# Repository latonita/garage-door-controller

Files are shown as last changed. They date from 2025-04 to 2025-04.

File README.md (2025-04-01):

# garage-door-controller
Garage door controller with integrated motor driver 24V/36V, 7A

Features:
- DRV8701 driver
   - selectable mosfet gate drive
   - and overcurrent protection
- PowerSO mosfets
  - shall be enough to run 24V/7A and more
- External interface for common RF-receivers
  - RX-480R / RF11A04 
  - HCS301 based
- Fabrication
  - Prepared for automated assembly on JLCPCB
  - Most of components are basic, no unnesessary Pick-and-place feeding fees. I personally order only couple of Extended parts to be soldered.

# under construction

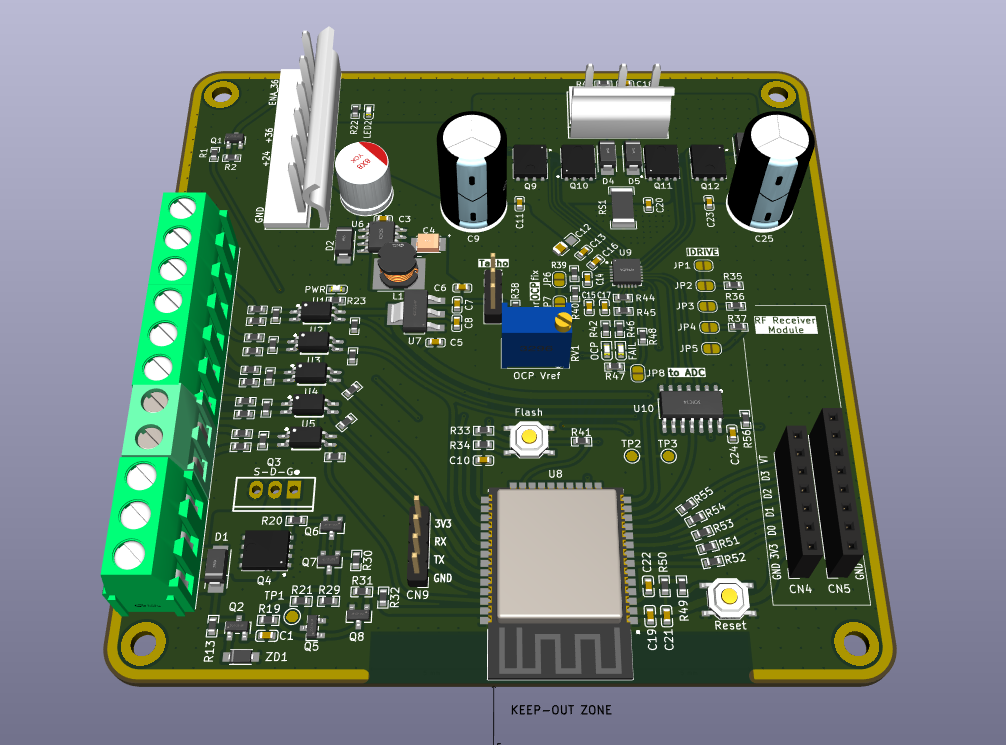
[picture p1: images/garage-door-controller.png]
Garage door controller PCB


# BOM

[Interactive BOM](https://raw.githack.com/latonita/garage-door-controller/refs/heads/main/kicad-project/bom/ibom.html)

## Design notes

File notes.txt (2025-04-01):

Tracks
 - signals mostly 0.25mm, some longer 0.3mm
 - power 0.5mm mostly

Clearance
 - 36V(VM) and motor planes - 0.6mm
 - GND 0.4mm

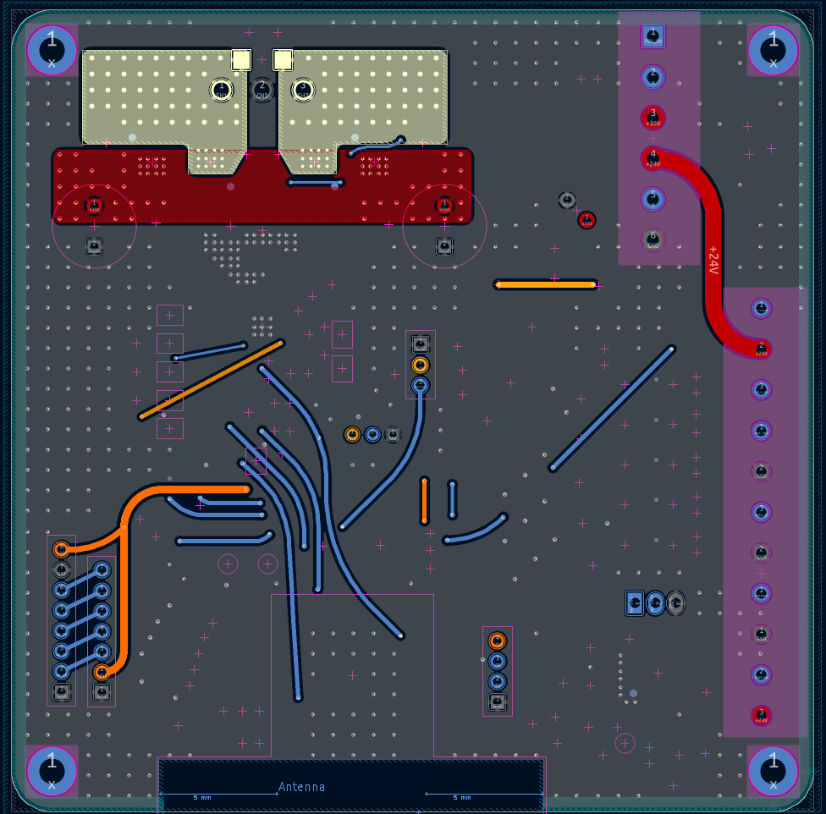
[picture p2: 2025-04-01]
images/pcb-bottom.png

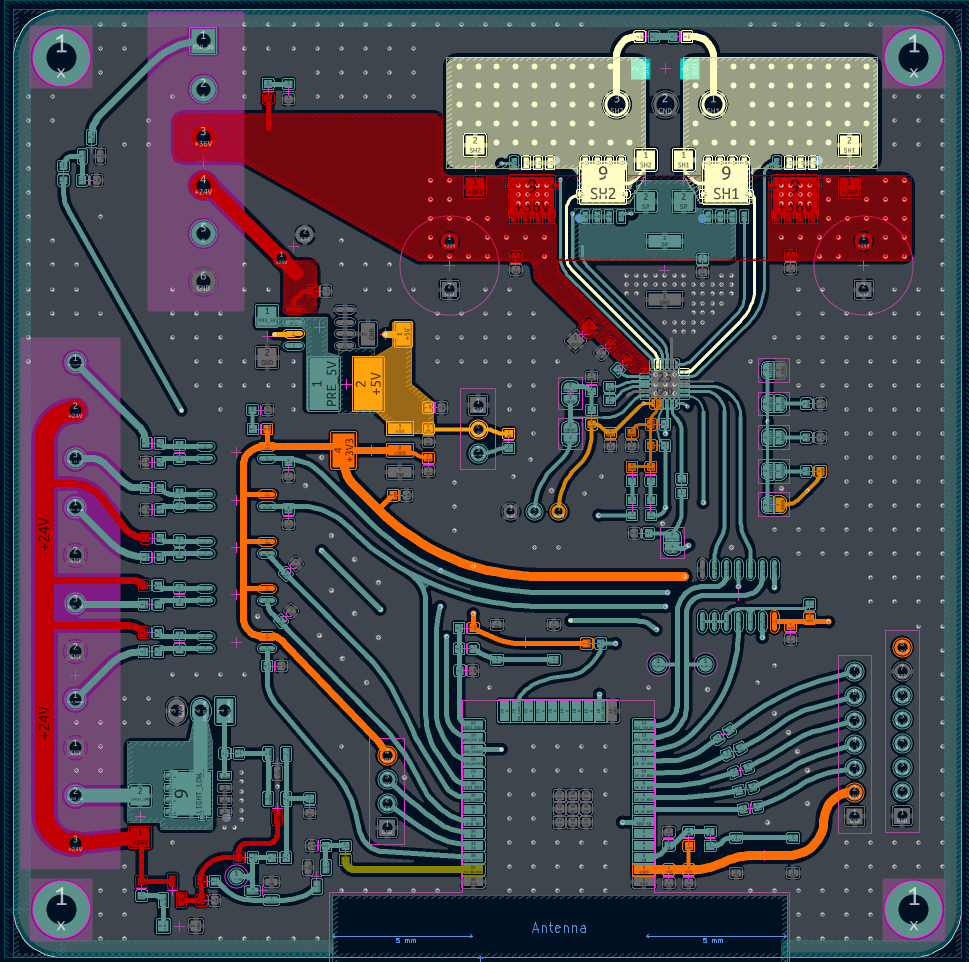
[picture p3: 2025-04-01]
images/pcb-top.png

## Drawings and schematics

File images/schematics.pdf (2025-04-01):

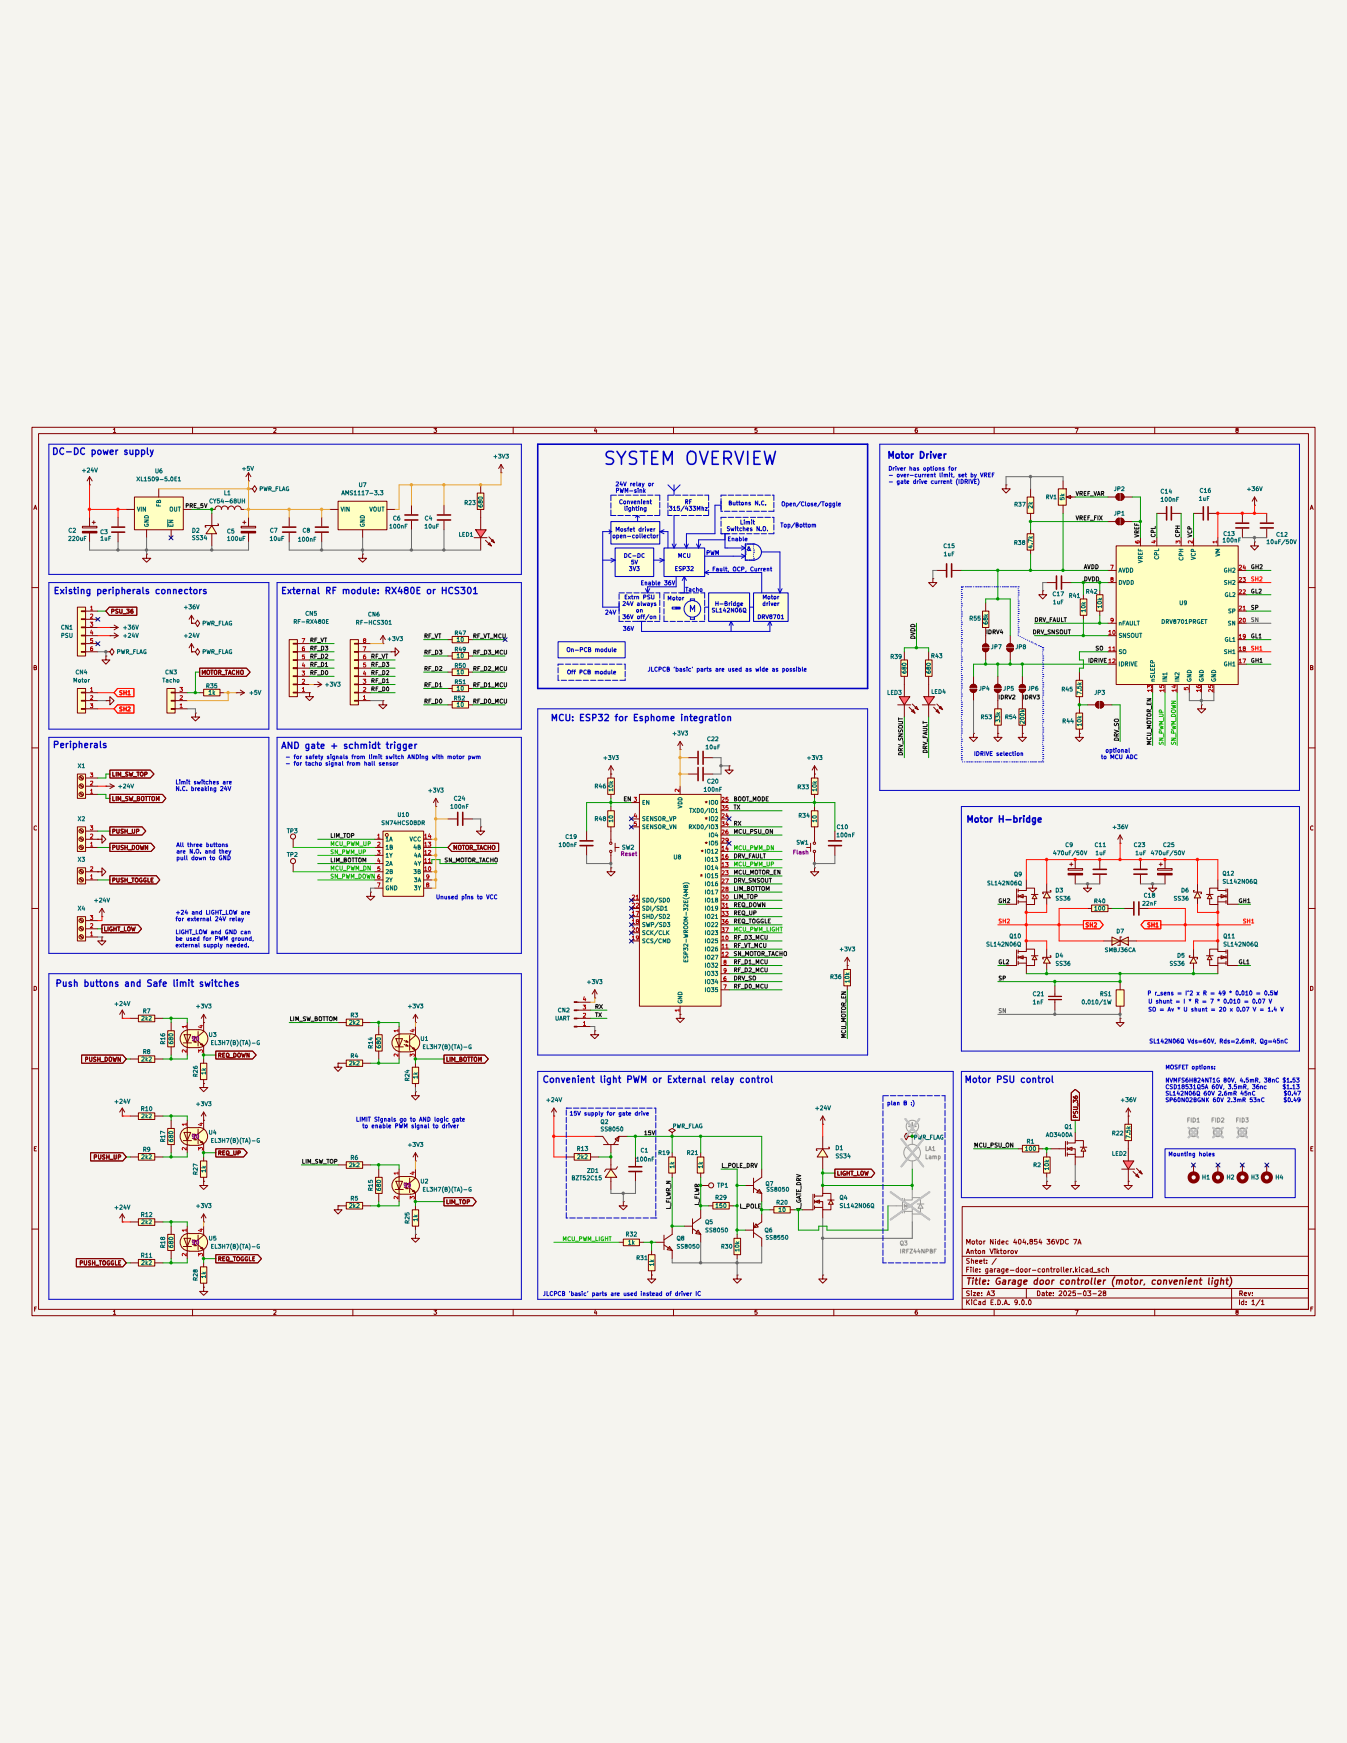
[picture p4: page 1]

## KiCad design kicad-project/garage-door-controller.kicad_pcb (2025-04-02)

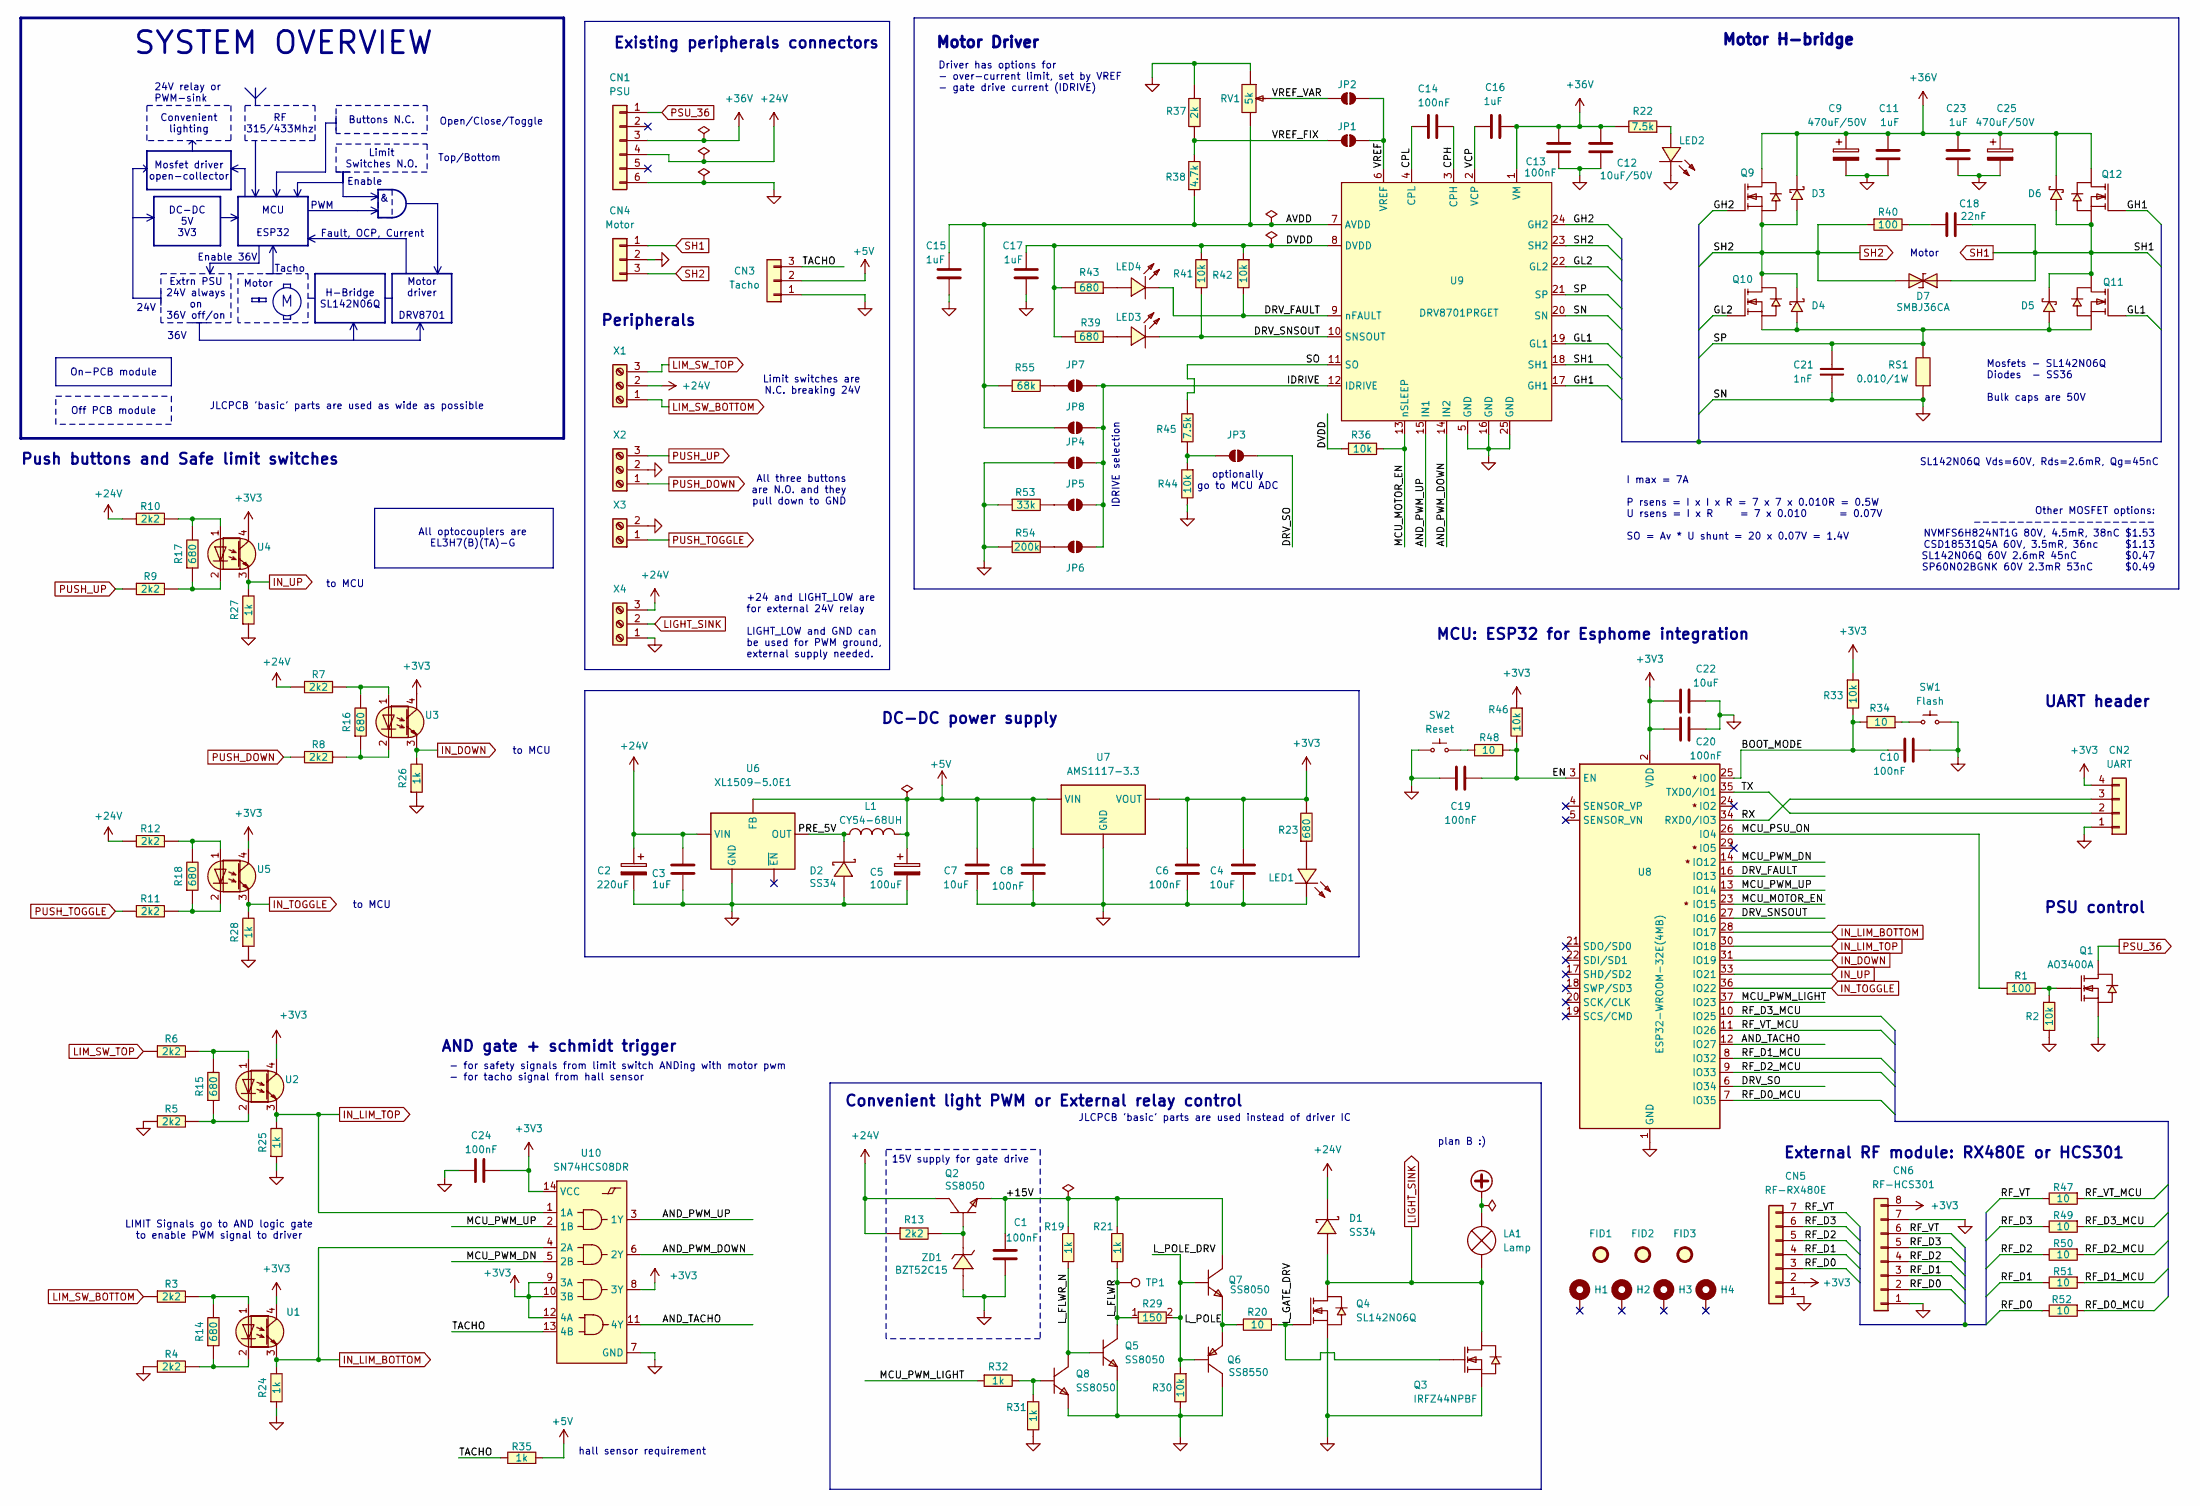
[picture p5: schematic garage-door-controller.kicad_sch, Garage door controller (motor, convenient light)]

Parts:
C1, C6, C8, C10, C13, C14, C19, C20, C24: 100nF; C0603; LCSC Part C14663
C2: 220uF; CAP-TH_BD8.0-P3.50-D0.6-FD; LCSC Part C106697
C3, C11, C15, C16, C17, C23: 1uF; C0603; LCSC Part C15849
C4, C7, C22: 10uF; C0603; LCSC Part C19702
C5: 100uF; CASE-B_3528; LCSC Part C16133
C9, C25: 470uF/50V; CAP-TH_BD10.0-P5.00-D1.0-FD; LCSC Part C88733
C12: 10uF/50V; C0805; LCSC Part C440198
C18: 22nF; C0603; LCSC Part C21122
C21: 1nF; C0603; LCSC Part C1588
CN1: PSU; CONN-TH_6P-P5.08_CH5.08-6A; LCSC Part C76512
CN2: UART; PinHeader_1x04_P2.54mm_Vertical
CN3: Tacho; PinHeader_1x03_P2.54mm_Vertical
CN4: Motor; CONN-TH_CH5.08-3A; LCSC Part C23514
CN5: RF-RX480E; PinSocket_1x07_P2.54mm_Vertical; LCSC Part C22438157
CN6: RF-HCS301; PinSocket_1x08_P2.54mm_Vertical; LCSC Part C27438
D1, D2: SS34; SMA_L4.3-W2.6-LS5.2-RD; LCSC Part C8678
D3, D4, D5, D6: SS36; SMA_L4.3-W2.6-LS5.2-RD; LCSC Part C16015
D7: SMBJ36CA; SMB_L4.6-W3.6-LS5.3-BI; LCSC Part C78421
FID1, FID2, FID3: Fiducial; Fiducial_1mm_Mask2mm
H1, H2, H3, H4: MountingHole; MountingHole_3.2mm_M3_DIN965_Pad
JP1, JP2, JP3, JP4, JP5, JP6, JP7, JP8: SolderJumper_2_Open; SolderJumper-2_P1.3mm_Open_RoundedPad1.0x1.5mm
L1: CY54-68UH; IND-SMD_L5.8-W5.2; LCSC Part C2929435
LA1: Lamp
LED1, LED2, LED3, LED4: KT-0603R; LED0603-RD; LCSC Part C2286
Q1: AO3400A; SOT-23-3_L2.9-W1.3-P1.90-LS2.4-BR; LCSC Part C20917
Q2, Q5, Q7, Q8: SS8050; SOT-23-3_L2.9-W1.3-P1.90-LS2.4-BR; LCSC Part C2150
Q3: IRFZ44NPBF; TO-220-3_L10.0-W4.5-P2.54-L; LCSC Part C2586
Q4, Q9, Q10, Q11, Q12: SL142N06Q; PDFN-8_L5.9-W5.2-P1.27-LS6.2-BL; LCSC Part C18208610
Q6: SS8550; SOT-23-3_L2.9-W1.3-P1.90-LS2.4-BR; LCSC Part C8542
R1, R40: 100; R0603; LCSC Part C22775
R2, R30, R33, R36, R41, R42, R44, R46: 10k; R0603; LCSC Part C25804
R3, R4, R5, R6, R7, R8, R9, R10, R11, R12, R13: 2k2; R0603; LCSC Part C4190
R14, R15, R16, R17, R18, R23, R39, R43: 680; R0603; LCSC Part C23228
R19, R21, R24, R25, R26, R27, R28, R31, R32, R35: 1k; R0603; LCSC Part C21190
R20, R34, R47, R48, R49, R50, R51, R52: 10; R0603; LCSC Part C22859
R22, R45: 7.5k; R0603; LCSC Part C23234
R29: 150; R0603; LCSC Part C22808
R37: 2k; R0603; LCSC Part C22975
R38: 4.7k; R0603; LCSC Part C23162
R53: 33k; R0603; LCSC Part C4216
R54: 200k; R0603; LCSC Part C25811
R55: 68k; R0603; LCSC Part C23231
RS1: 0.010/1W; R2512; LCSC Part C393072
RV1: 5k; RES-ADJ-TH_3296W; LCSC Part C60620
SW1, SW2: TS-1187A-B-A-B; SW-SMD_4P-L5.1-W5.1-P3.70-LS6.5-TL_H1.5; LCSC Part C318884
TP1: TestPoint; TestPoint_Pad_D1.5mm
U1, U2, U3, U4, U5: EL3H7(B)(TA)-G; SOP-4_L4.4-W2.8-P1.27-LS7.0-TL; LCSC Part C32565
U6: XL1509-5.0E1; SOIC-8_L5.0-W4.0-P1.27-LS6.0-BL; LCSC Part C61063
U7: AMS1117-3.3; SOT-223-3_L6.5-W3.4-P2.30-LS7.0-BR; LCSC Part C6186
U8: ESP32-WROOM-32E(4MB); WIFI-SMD_ESP32-WROOM-32E; LCSC Part C701341
U9: DRV8701PRGET; VQFN-24_L4.0-W4.0-P0.50-TL-EP2.8; LCSC Part C2150478
U10: SN74HCS08DR; SOIC-14_L8.7-W3.9-P1.27-LS6.0-BL; LCSC Part C2868021
X1, X2, X4: WJ500V-5.08-3P-14-00A; CONN-TH_3P-P5.00_WJ500V-5.08-3P; LCSC Part C72334
X3: WJ500V-5.08-2P-14-00A; CONN-TH_2P-P5.00_WJ500V-5.08-2P; LCSC Part C8465
ZD1: BZT52C15; SOD-123_L2.7-W1.6-LS3.8-RD; LCSC Part C2932746

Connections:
+3V3: C4.2, C6.2, C20.1, C22.1, C24.1, CN2.4, CN5.2, CN6.8, R23.2, R33.1, R46.1, U1.4, U2.4, U3.4, U4.4, U5.4, U7.2 (VOUT), U7.4 (TAB), U8.2 (VDD), U10.8 (3Y), U10.9 (3A), U10.10 (3B), U10.12 (4A), U10.14 (VCC)
+5V: C5.1, C7.2, C8.2, CN3.2, L1.2, R35.1, U6.3 (FB), U7.3 (VIN)
+24V: C2.1, C3.2, CN1.4, D1.1 (K), Q2.3 (C), R7.1, R10.1, R12.1, R13.1, U6.1 (VIN), X1.2, X4.3
+36V: C9.1, C11.2, C12.2, C13.1, C16.2, C23.2, C25.1, CN1.3, D3.1 (K), D6.1 (K), Q9.5 (D), Q9.6 (D), Q9.7 (D), Q9.8 (D), Q9.9 (D), Q12.5 (D), Q12.6 (D), Q12.7 (D), Q12.8 (D), Q12.9 (D), R22.2, U9.1 (VM)
/+15V: C1.2, Q2.2 (E), Q7.3 (C), R19.2, R21.2
/AND_PWM_DOWN: U9.14 (IN2), U10.6 (2Y)
/AND_PWM_UP: U9.15 (IN1), U10.3 (1Y)
/AND_TACHO: U8.12 (IO27), U10.11 (4Y)
/AVDD: C15.2, JP8.1 (A), R38.1, R55.1, RV1.1, U9.7 (AVDD)
/BOOT_MODE: C10.1, R33.2, R34.2, U8.25 (IO0)
/CPH: C14.1, U9.3 (CPH)
/CPL: C14.2, U9.4 (CPL)
/DRV_FAULT: LED4.1 (K), R42.2, U8.16 (IO13), U9.9 (nFAULT)
/DRV_SNSOUT: LED3.1 (K), R41.2, U8.27 (IO16), U9.10 (SNSOUT)
/DRV_SO: JP3.1 (A), U8.6 (IO34)
/DVDD: C17.2, R36.1, R39.2, R41.1, R42.1, R43.2, U9.8 (DVDD)
/EN: C19.1, R46.2, R48.1, U8.3 (EN)
/GH1: Q12.4 (G), U9.17 (GH1)
/GH2: Q9.4 (G), U9.24 (GH2)
/GL1: Q11.4 (G), U9.19 (GL1)
/GL2: Q10.4 (G), U9.22 (GL2)
/IDRIVE: JP4.2 (B), JP5.2 (B), JP6.2 (B), JP7.2 (B), JP8.2 (B), U9.12 (IDRIVE)
/L_FLWR: Q5.3 (C), R21.1, R29.1, TP1.1
/L_FLWR_N: Q5.1 (B), Q8.3 (C), R19.1
/L_GATE_DRV: Q3.1 (G), Q4.4 (G), R20.1
/L_POLE: Q6.2 (E), Q7.2 (E), R20.2
/L_POLE_DRV: Q6.1 (B), Q7.1 (B), R29.2, R30.1
/MCU_MOTOR_EN: R36.2, U8.23 (IO15), U9.13 (nSLEEP)
/MCU_PSU_ON: R1.1, U8.26 (IO4)
/MCU_PWM_DN: U8.14 (IO12), U10.5 (2B)
/MCU_PWM_LIGHT: R32.1, U8.37 (IO23)
/MCU_PWM_UP: U8.13 (IO14), U10.2 (1B)
/PRE_5V: D2.1 (K), L1.1, U6.2 (OUT)
/RF_D0: CN5.3, CN6.2, R52.2
/RF_D0_MCU: R52.1, U8.7 (IO35)
/RF_D1: CN5.4, CN6.3, R51.2
/RF_D1_MCU: R51.1, U8.8 (IO32)
/RF_D2: CN5.5, CN6.4, R50.2
/RF_D2_MCU: R50.1, U8.9 (IO33)
/RF_D3: CN5.6, CN6.5, R49.2
/RF_D3_MCU: R49.1, U8.10 (IO25)
/RF_VT: CN5.7, CN6.6, R47.2
/RF_VT_MCU: R47.1, U8.11 (IO26)
/RX: CN2.3, U8.34 (RXD0/IO3)
/SO: R45.2, U9.11 (SO)
/SP: C21.2, D4.2 (A), D5.2 (A), Q10.1 (S), Q10.2 (S), Q10.3 (S), Q11.1 (S), Q11.2 (S), Q11.3 (S), RS1.2, U9.21 (SP)
/TACHO: CN3.3, R35.2, U10.13 (4B)
/TX: CN2.2, U8.35 (TXD0/IO1)
/VCP: C16.1, U9.2 (VCP)
/VREF: JP1.2 (B), JP2.2 (B), U9.6 (VREF)
/VREF_FIX: JP1.1 (A), R37.2, R38.2
/VREF_VAR: JP2.1 (A), RV1.2
GND: C1.1, C2.2, C3.1, C4.1, C5.2, C6.1, C7.1, C8.1, C9.2, C10.2, C11.1, C12.1, C13.2, C15.1, C17.1, C19.2, C20.2, C21.1, C22.2, C23.1, C24.2, C25.2, CN1.6, CN2.1, CN3.1, CN4.2, CN5.1, CN6.1, CN6.7, D2.2 (A), JP4.1 (A), LED1.1 (K), LED2.1 (K), Q1.2 (S), Q3.3 (S), Q4.1 (S), Q4.2 (S), Q4.3 (S), Q5.2 (E), Q6.3 (C), Q8.2 (E), R2.2, R4.1, R5.1, R24.1, R25.1, R26.1, R27.1, R28.1, R30.2, R31.1, R37.1, R44.2, R53.1, R54.1, RS1.1, RV1.3, SW1.1 (A), SW1.2 (B), SW2.1 (A), SW2.2 (B), U6.5 (GND), U6.6 (GND), U6.7 (GND), U6.8 (GND), U7.1 (GND), U8.1 (GND), U8.15 (GND), U8.38 (GND), U8.39 (GND), U9.5 (GND), U9.16 (GND), U9.20 (SN), U9.25 (GND), U10.7 (GND), X2.2, X3.2, X4.1, ZD1.2 (A)
IN_DOWN: R26.2, U3.3, U8.31 (IO19)
IN_LIM_BOTTOM: R24.2, U1.3, U8.28 (IO17), U10.4 (2A)
IN_LIM_TOP: R25.2, U2.3, U8.30 (IO18), U10.1 (1A)
IN_TOGGLE: R28.2, U5.3, U8.36 (IO22)
IN_UP: R27.2, U4.3, U8.33 (IO21)
LIM_SW_BOTTOM: R3.1, X1.1
LIM_SW_TOP: R6.1, X1.3
unnamed: C18.1, R40.2
unnamed: JP3.2 (B), R44.1, R45.1
unnamed: JP5.1 (A), R53.2
unnamed: JP6.1 (A), R54.2
unnamed: JP7.1 (A), R55.2
unnamed: LED1.2 (A), R23.1
unnamed: LED2.2 (A), R22.1
unnamed: LED3.2 (A), R39.1
unnamed: LED4.2 (A), R43.1
unnamed: Q1.1 (G), R1.2, R2.1
unnamed: Q2.1 (B), R13.2, ZD1.1 (K)
unnamed: Q8.1 (B), R31.2, R32.2
unnamed: R10.2, R17.2, U4.1
unnamed: R11.2, R18.1, U5.2
unnamed: R12.2, R18.2, U5.1
unnamed: R4.2, R14.1, U1.2
unnamed: R3.2, R14.2, U1.1
unnamed: R5.2, R15.1, U2.2
unnamed: R6.2, R15.2, U2.1
unnamed: R8.2, R16.1, U3.2
unnamed: R7.2, R16.2, U3.1
unnamed: R9.2, R17.1, U4.2
unnamed: R34.1, SW1.3 (C), SW1.4 (D)
unnamed: R48.2, SW2.3 (C), SW2.4 (D)
PSU_36: CN1.1, Q1.3 (D)
PUSH_DOWN: R8.1, X2.1
PUSH_TOGGLE: R11.1, X3.1
PUSH_UP: R9.1, X2.3
SH1: C18.2, CN4.1, D5.1 (K), D6.2 (A), D7.1 (K), Q11.5 (D), Q11.6 (D), Q11.7 (D), Q11.8 (D), Q11.9 (D), Q12.1 (S), Q12.2 (S), Q12.3 (S), U9.18 (SH1)
SH2: CN4.3, D3.2 (A), D4.1 (K), D7.2 (A), Q9.1 (S), Q9.2 (S), Q9.3 (S), Q10.5 (D), Q10.6 (D), Q10.7 (D), Q10.8 (D), Q10.9 (D), R40.1, U9.23 (SH2)

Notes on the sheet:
JLCPCB 'basic' parts are used as wide as possible
All optocouplers are EL3H7(B)(TA)-G
Motor H-bridge
Top/Bottom
Enable
Other MOSFET options: --------------------- NVMFS6H824NT1G 80V, 4.5mR, 38nC $1.53 CSD18531Q5A 60V, 3.5mR, 36nc $1.13 SL142N06Q 60V 2.6mR 45nC $0.47 SP60N02BGNK 60V 2.3mR 53nC $0.49
IDRIVE selection
DC-DC power supply
Peripherals
Tacho
36V
PSU control
hall sensor requirement
to MCU
JLCPCB 'basic' parts are used instead of driver IC
Motor
Enable 36V
SYSTEM OVERVIEW
Existing peripherals connectors
All three buttons are N.O. and they pull down to GND
MCU: ESP32 for Esphome integration
plan B :)
optionally go to MCU ADC
Driver has options for - over-current limit, set by VREF - gate drive current (IDRIVE)
PWM
Fault, OCP, Current
Mosfets - SL142N06Q Diodes - SS36 Bulk caps are 50V
Convenient light PWM or External relay control
+24 and LIGHT_LOW are for external 24V relay LIGHT_LOW and GND can be used for PWM ground, external supply needed.
UART header
Limit switches are N.C. breaking 24V
Open/Close/Toggle
SL142N06Q Vds=60V, Rds=2.6mR, Qg=45nC
AND gate + schmidt trigger
External RF module: RX480E or HCS301
24V relay or PWM-sink
- for safety signals from limit switch ANDing with motor pwm - for tacho signal from hall sensor
24V
I max = 7A P rsens = I x I x R = 7 x 7 x 0.010R = 0.5W U rsens = I x R = 7 x 0.010 = 0.07V SO = Av * U shunt = 20 x 0.07V = 1.4V
LIMIT Signals go to AND logic gate to enable PWM signal to driver

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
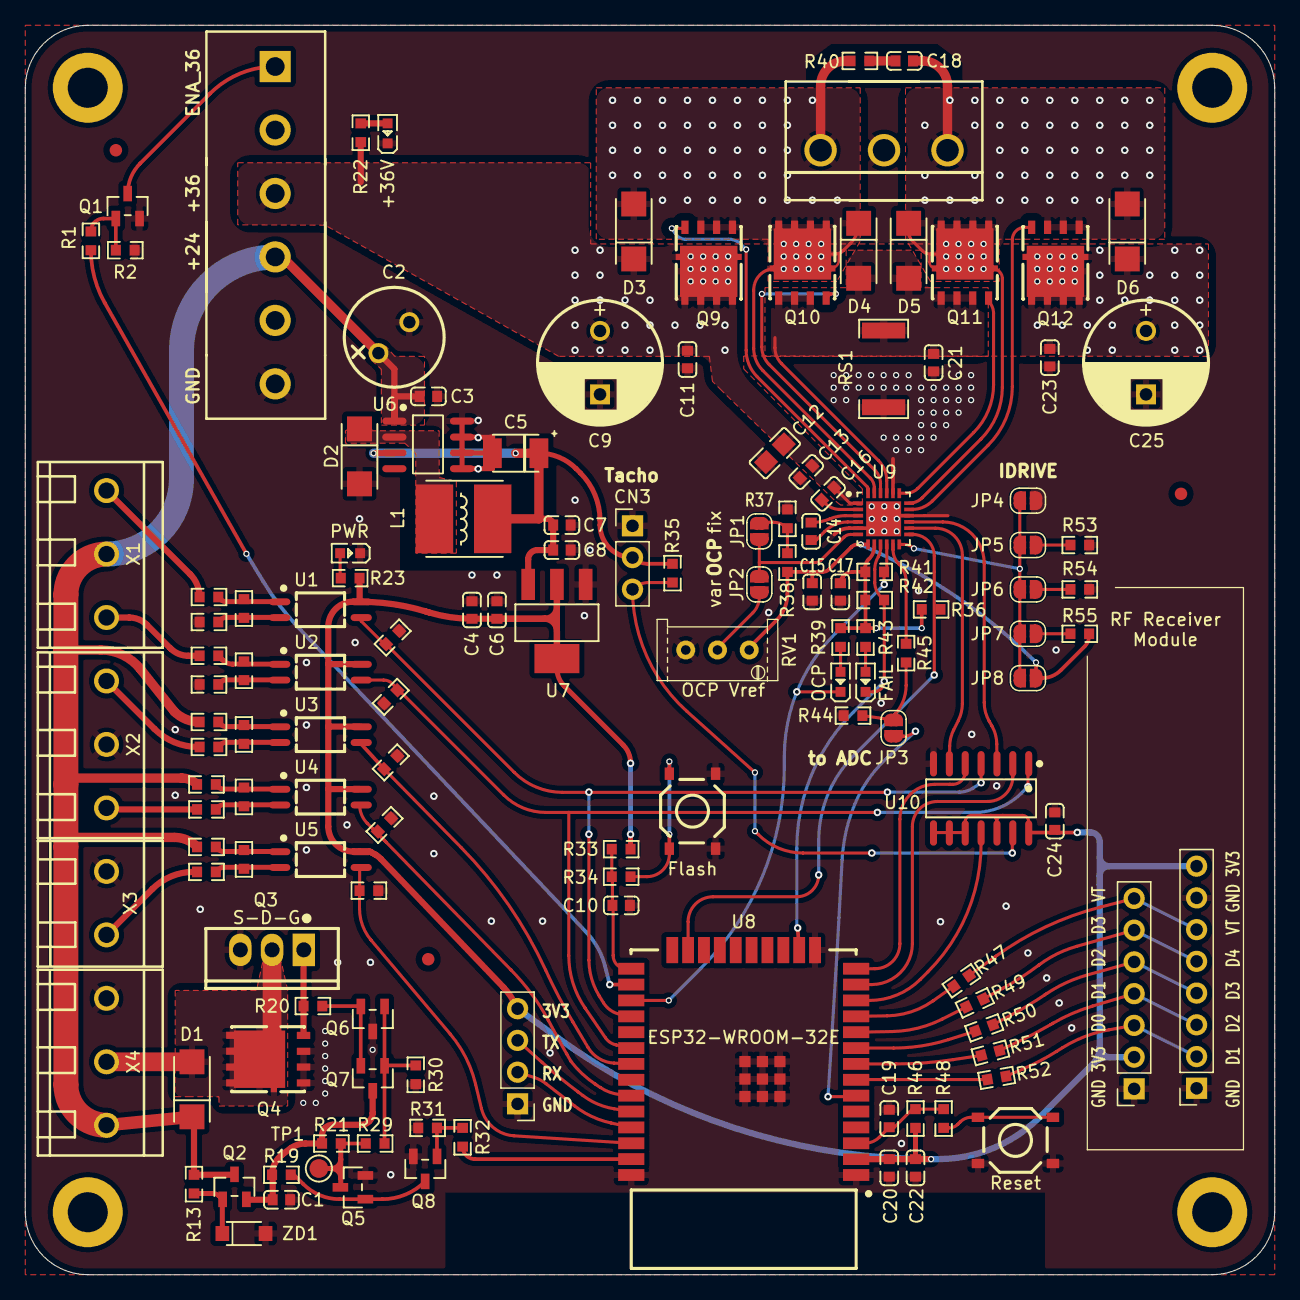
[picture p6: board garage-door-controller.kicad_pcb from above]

Board: 2 copper layers, 100.0 x 100.0 mm, 145 parts (1 on the bottom side), 91 nets.
